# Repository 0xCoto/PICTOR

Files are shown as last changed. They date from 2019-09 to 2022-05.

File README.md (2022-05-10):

# PICTOR: A free-to-use Radio Telescope
PICTOR is an open-source radio telescope that allows anyone to observe the radio sky, using its convenient web platform for free: https://www.pictortelescope.com

The PICTOR Radio Telescope

The PICTOR Radio Telescope

## About PICTOR
PICTOR consists of a 1.5-meter parabolic antenna that allows anyone to make continuous and spectral (i.e. [hydrogen line](https://en.wikipedia.org/wiki/Hydrogen_line)) drift-scan observations of the radio sky in the **1300~1700 MHz** regime for free. 

The goal of this effort is to introduce students, educators, astronomers and others to the majesty of the radio sky, **promoting radio astronomy education**, *without* the need of building a large and expensive radio telescope. 

PICTOR is a **fully open source** (software & hardware) project.

## Northern Sky HI Survey obtained with PICTOR
PICTOR HI Survey

## Technical Details (Telescope Specifications)
**Telescope diameter:** 1.5m (4.92 ft = 59.05")  
**Focal Ratio (F/D):** 0.411 (prime focus antenna)  
**Beamwidth (HPBW @ 1420 MHz):** \~8.95° (*k* factor = 63.64)  
**Operating frequency range:** 1300\~1700 MHz ([L band](https://en.wikipedia.org/wiki/L_band))  
**Two-stage low-noise amplifier (LNA):** Gain: 30 ± 2 dB - Noise figure (NF): < 0.5 dB  
**High-pass filter:** -30 dBc below 900 MHz  
~~**Third-stage LNA (used as an in-line amplifier):** Gain: > 9 dB~~ *  
~~**Band-pass filter:** f_center = 1420 MHz (designed for [hydrogen line](https://en.wikipedia.org/wiki/Hydrogen_line) observations)~~ *  
**Instantaneous bandwidth (IBW):** up to 3.2 MHz (sufficient for spectral observations) *[to be upgraded to 30.72 MHz]*  
**Number of channels:** up to 2048 (for high frequency-resolution observations) *[to be upgraded to 16384]*  

*\*Deemed unnecessary hence removed*

## Telescope Block Diagram
Telescope Block Diagram

## PICTOR System Flowgraph
PICTOR flowgraph

## GRC Data Acquisition Flowgraph (old)
Data Acquisition Flowgraph (old)

## GRC Data Acquisition Flowgraph (4-tap weighted overlap-add (WOLA) Fourier transform spectrometer)
Data Acquisition Flowgraph

## Feedhorn Dimensions
Feedhorn dimensions

## S-Parameters
S-Parameter of the monopole inside the feed:
S-Parameter of the monopole

S-Parameter of the feedhorn (with rod) - **this should be the considered S-Parameter of the antenna in its entirety**:
S-Parameter of the feedhorn

Measured with the **Keysight N5221A PNA Network Analyzer (10 MHz~13.5 GHz)**:
Measurement of the monopole at the lab
Measurement of the feedhorn at the lab

## Example Observation
Example Observation

## Wish to observe with PICTOR?
Take a look at the [PDF guide](https://www.pictortelescope.com/Observing_the_radio_sky_with_PICTOR.pdf) containing all the information you need to know in order to conduct your first observation of the radio sky!

<p align="center">
  PICTOR Telescope Logo
</p>

## A description/role for each file
File | Description
--- | --- 
`observe.py` | Listens for observation requests & conducts observations
`plot.py` | Produces plots from observation data
`plot_hi.py` | Produces HI-tailored plots (i.e. +calibrated spectrum) from observation data
`id_history.txt` | Serves as an observation ID history database
`fft_integration.grc` | [GRC](https://wiki.gnuradio.org/index.php/GNURadioCompanion) Flowgraph previously used for the recording and processing of the data
`top_block_old.py` | Embedded Python Block for `fft_integration.grc`
`pfb.grc` | [GRC](https://wiki.gnuradio.org/index.php/GNURadioCompanion) Polyphase Filterbank Flowgraph for efficient data acquisition
`top_block.py` | Embedded Python Block for `pfb.grc`
`observe.php` | Includes server-side PHP code for [/observe](https://www.pictortelescope.com/observe)
`Waveguide.stl` | STL file for feedhorn visualization

## Credits
**PICTOR** was built by **[Apostolos Spanakis-Misirlis](https://www.github.com/0xCoto)**.

Special thanks to **Dr. Cameron Van Eck** for his thorough guidance throughout the development of PICTOR, the **[Telecommunication Systems Laboratory](http://tsl.ds.unipi.gr/)** of the [Department of Digital Systems](https://www.ds.unipi.gr/en/) at the [University of Piraeus](https://www.unipi.gr/unipi/en/) for allowing us to conduct decisive antenna measurements, the [Dwingeloo Radio Observatory](https://www.camras.nl/en/) (**Paul Boven** & **Dr. Cees Bassa**) for helping with the recording & the plotting of the data, **[Vasilis Spanakis-Misirlis](mailto:meiko_dew@hotmail.com)** for his engineering assistance, Konstantinos Bakolitsas for his support and **[ynk](https://www.github.com/ynk)** & **[Tino](https://www.github.com/RononDex/)** for their back-end contribution to `observe.php`.

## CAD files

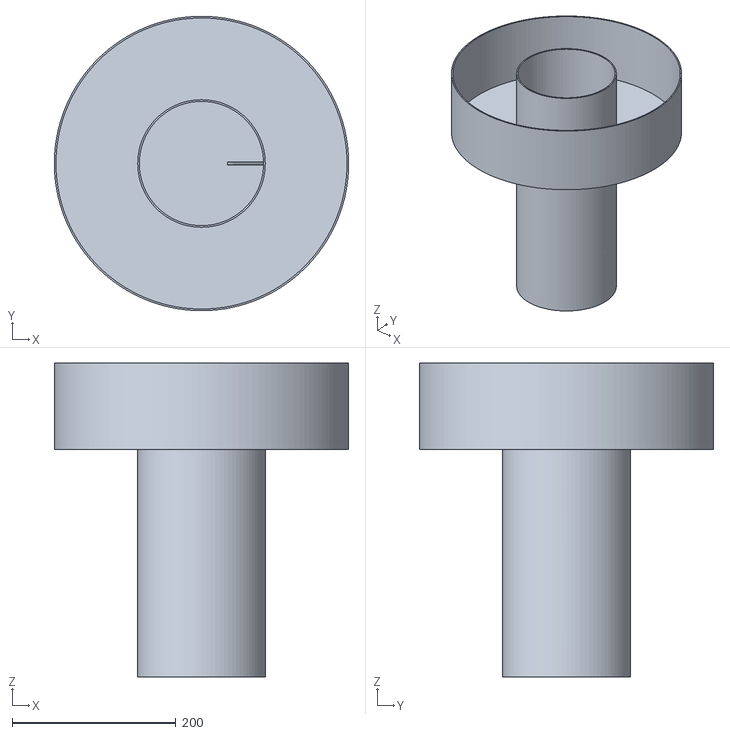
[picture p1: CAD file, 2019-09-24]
Waveguide.stl
360.0 x 359.9 x 384.0

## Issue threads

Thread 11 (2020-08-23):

Send Raw Data

ministerofsillywalks, 2020-08-23:
Hi! One thing that I've felt was missing from the PICTOR experience was the ability to have the raw data. It's nice to quickly see the results of an observation, but it's hard to do precise analysis of the data. Would it be possible to have an option when you submit the obs. request to receive the raw data file, perhaps in a csv file, for each of the graphs?

0xCoto, 2020-08-23:
Hey, thanks for your feedback! I suppose that's possible, but it requires a bit of work from my side (feel free to contribute if you'd really wanna see that - hint: you'll have to add a relevant checkbox option to [`observe.php`](https://github.com/0xCoto/PICTOR/blob/master/observe.php) and edit [`observe.py`](https://github.com/0xCoto/PICTOR/blob/master/observe.py) to permit the server (pictortelescope.com) and the client (telescope) to share that parameter).

However, I am more than happy to send you the raw data of your observation, given your Observation ID. If you look at [line 120](https://github.com/0xCoto/PICTOR/blob/master/observe.py#L120-L164) of `observe.py`, you'll notice that I keep a copy of every observation's raw data (`.dat` file), so if a user wishes to process, analyze and inspect their data in greater detail, they have the freedom to do so.

The reason I don't include the `.dat` in the original email is to avoid confusion, as many users are unfamiliar with Python to run `plot.py`, nor do they understand how radio astronomy digital signal processing/data analysis works.

But if you think this is worth implementing, it's an easy code change, so I could probably find some time to implement it.

ministerofsillywalks, 2020-08-24:
I have an idea about how to do this, but I have a couple of questions about the system:
1. If all the observation parameters are stored and read from `last_obs.txt`, what is `last_obs_duration.txt` used for?
2. Can I use a package that has not been used yet? specifically, pandas.
Thanks!

0xCoto, 2020-08-24:
1. Short answer: user privacy. The telescope fetches `last_obs.txt`, but the website (`observe.php`) needs to fetch the last observation request datetime and duration. This was initially used to check if an observation was already running to prevent clogging from observation requests. The reason it doesn’t just fetch `last_obs.txt` is because that file includes the email address of the observer, which is sensitive data, which is obviously a problem, both ethically and legally (GDPR).

2. For plotting? You can use anything you like of course, but I’d be curious to know what you’d like to play with that `plot.py`/`plot_hi.py` and numpy doesn’t already provide.

ministerofsillywalks, 2020-08-24:
I want to use pandas to save csv files because it allows you to save with each data array in a labeled column easily, whereas if I just used numpy to write csv's it would be messier. Taking it a step back, I would rather make csv files in addition to the .dat file because the csv's are easier to open. Basically I'm trying to make it as easy as possible to get good data.

P.S. If it's not too big a problem, could you send me the dat file for observation 55275982 so I can test my code? This is one of my own observations. Thanks!

0xCoto, 2020-08-25:
You should be able to do this with numpy as well. I've implemented something like this for `.txt`, but you should be able to adjust it for `.csv` formatting as well pretty easily, but feel free to use whatever is more convenient for you of course.

Example snippet for saving the calibrated spectrum (you place this in `plot_hi.py`):
```python
np.savetxt('freq.txt', freq, delimiter='\n', fmt='%1.3f')
np.savetxt('snr.txt', estimate_S_N_simple(spectrum, mask), delimiter='\n', fmt='%1.3f')
```

I've uploaded your `observation.dat` file [here](https://gofile.io/d/d4AVVo).

ministerofsillywalks, 2020-08-26:
Thanks for the file! I just created the pull request.

Closed 2020-09-20.

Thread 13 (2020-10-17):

Transpose data in CSV files

andy8025, 2020-10-17:
Change the way data are stored in __data_spectrum.csv__ and __data_time_power.csv__ files that are emailed to user. Transpose rows and columns - to store samples in rows instead of columns.

Current layout:

foo|1000|1001|1002|...
------------ | ------------- | ------------- | ------------- | -------------
__bar__|__2000__|__2001__|__2002__|__...__

Proposed layout:

foo|bar
------------ | -------------
__1000__|__2000__
__1001__|__2001__
__1002__|__2002__
__...__|__...__

Current CSV file layout prevents LibreOffice Calc from reading all the data. LibreOffice error: "The data could not be loaded completely because the maximum number of columns per sheet was exceeded".

andy8025, 2020-10-17:
Made changes to __plot.py__ and __plot_hi.py__ to save the new transposed CSV files, in addition to the original CSV files. Did not modify the code in __observe.py__ that emails the CSV files.

Don't know how to check what Python libraries are available on the actual telescope system.  I see that NumPy is available, hope that Pandas is available as well :)

ministerofsillywalks, 2020-10-17:
When I first did this, I wanted to use pandas to make the CSVs the way you want them, @0xCoto asked that I stick with just numpy instead.

ministerofsillywalks, 2020-10-17:
You might be able to use np.transpose() https://note.nkmk.me/en/python-numpy-transpose/ without importing pandas.

ministerofsillywalks, 2020-10-18:
You shouldn't need pandas because you can do the transposition without reopening the csvs, just do it before they are saved.

andy8025, 2020-10-18:
Ok, I can try it in numpy.  Is it possible to get a copy of __observation.dat__, so that I may generate the __data_freq_zmean__ and __data_t_w__ numpy arrays?

0xCoto, 2020-10-18:
Thanks for the PR, just approved! The changes have been applied to the telescope, so feel free to try it out. :)

Closed 2020-10-18.

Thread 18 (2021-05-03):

Time Series File showing Power to 3DP

davewyers, 2021-05-03:
Hi There

Love your work.  I have a 2.3M dish that I have planning on going live with VIRGO in a couple of weeks, meanwhile I was generating some data with PICTOR to play with.

I ran a test on Pictor and when I looked at the Time Series data it appears that the Relative Power column is only showing 3DP "0.010" across all time time slots.  I am assuming that Column 1 is Time & Column 2 is Relative Power.

The graph is displaying values to 6DP.

See below.

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

0xCoto, 2021-05-03:
Thanks for the feedback!

davewyers, 2021-05-04:
Perfect, I have just tested and can confirm the fix.

What is the best way to interact around PICTOR & VIRGO outside of issues, do you have a user forum?

Regards
Dave

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

0xCoto, 2021-05-05:
There used to be a Discourse page (forum) for discussions related to PICTOR and (radio) astronomy, but maintenance was a bit costly (mostly in terms of my time, and partially hosting costs as CPU allocation is higher hosting more web pages online).

davewyers, 2021-05-06:
Ok understood, thanks

Closed 2021-05-06.

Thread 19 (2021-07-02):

Comment batch (Richard K Collins)

0xCoto, 2021-07-02:
Full list of comments here: https://theinternetfoundation.net/?p=1742

0xCoto, 2021-07-02:
My response to every single comment is stated below. I skipped some minor parts because virtually identical replies have already been provided. Thanks to Richard Collins for the comments. Anyone wishing to resolve some of the commented requests is welcome to submit a pull request with the corresponding changes/additions.

---

> Please leave the settings and all form fields. Don’t clear them. Just leave them the same as the last observation.

This is not very easy if you consider there are many unique observers who wish to run observations with varying parameters. Leaving them the same as the last observation could introduce a lot of confusion between unique users visiting the website after one's observation. PICTOR does not make use of cookies for such things, but perhaps it could. It's a technical challenge though, and I do not know how much effort is worth putting into.

> I am having to re-enter them ever time I make a request.  I am making series of requests.  Many people might.

A simple trick to achieve this is to click `Observe` (the button), opening it in a new tab. This will submit the request, while leaving your fields in place. Maybe this helps as a quick solution.

> Tell them how many files they will receive, how many records per file, and the units and purpose.

The fundamentals regarding the expected results and how to interpret them are described in the [introductory PICTOR PDF](https://pictortelescope.com/Observing_the_radio_sky_with_PICTOR.pdf), but I agree that the CSV results may not be very clear, partially due to missing headers. Most users only look at the image plots though (not that this is a justification for lacking clarifications, but the point of PICTOR is to make observations easy for users with little to no experience, who just wish to see the results without much further processing work). As for the units, "relative power" highlights that the power is not calibrated to Kelvins or Janskys. This is imposed by an instrumentation limitation (requiring external noise source). But absolute measurements don't appear to be a necessity for most users who simply wish to detect clouds of neutral hydrogen etc.

> Put column headers in the csv files. You can add headers to explain the columns by using a # in the first column to indicate header...

I agree this would be useful.

> ...then use tab separators. Use tab separators through out. That is the default for Excel, even if they still say “csv”.

Virtually all CSV-formatted files I have seen use commas and not tabs. Transforming to tabs would annoy developers and programming libraries that are used to the more traditional **comma-separated** value format. I also don't understand what "default for Excel" means, because importing and exporting to CSV (with commas) is fully supported by common spreadsheet tools as far as I'm aware.

> CSV is NOT a standard.

The objective is to mimic a format as closely to what most users are familiar with as possible. The goal is for the interpretation of the results to be clear to the user and for the data to be easily parsable to other data-analysis software. This is also completely possible with **tab-separated** values (TSV), but less common than CSV handling.

> When you copy and paste from Excel, it is tab separated – because then you don’t have to write infinite recursion for quoted strings. Just a single tab between fields, line feed separating records. Human and Excel readable header lines.

As mentioned, you can import from and export to CSV with common spreadsheet software like Excel without problems. What format Excel decides to encode your clipboard in when you copy cells appears irrelevant, because it is intended for transferring data within the same type of software (spreadsheets). The incompatibility with programmatic data analysis (e.g. using Python libraries) becomes more apparent when trying to deal with TSV instead of CSV-formatted files.

> Show the consequences of choices. How many data points in the time series will be given for the selection?

This could be displayed with JavaScript on the spot; requires work though.

> What are the limits for your processor?

The available results have all been tested and supported, so the user does not need to worry about this to be worth mentioning.

> How fast could you provide small FFT records.

I assume this refers to the time-series delta t (Δt). There is a limit put in place (number of bins ≥ 100). The users cannot violate this and are informed if they try setting a value lower than that. This ensures that the machine does not struggle with processing and analyzing very large files, or uploading large chunks of data over the network.

> You show the waterfall but do not provide that time series.

Time-series (power vs time) is displayed at the bottom. If you are referring to raw time-domain I/Q information, each observation would be dramatically larger in data size, which would cause problems partially mentioned in the previous statement. The total size of an observation would be equal to `2` [I + Q channels] x `sample_rate` [samples/sec] x `8` [bits] x `duration` [sec].

> If someone is looking at adjacent frequencies to the center, you are only providing summary statistics.

It is not clear at all what this comment implies, nor what 'summary statistics' are. All information the user requires for typical hydrogen line observations is there, including the waterfall, average spectrum and calibrated (passband-corrected) spectrum.

> “Raw” means the original readings. What you are providing is a summary statistics in your time series. A computed value based on the FFT, which comes from the sampled time series data. “Raw” would be the 2.4 MegaSamplesPerSeconds or whatever the user selected. It could be requested — without FFT processing.

"Raw" may sound misleading to hint I/Q data, but it is in no way a strictly incorrect term. "Raw" is displayed in the sense that the data attached in the CSV are less processed. This includes the calibration/OFF spectrum (not calibrated), permitting the user to do manual passband calibrations. Feel free to propose a more appropriate adjective than "raw" that is more clear and I'll implement the modification.

> You might want to call the time series you provide now “Power time series” or “Relative Power time series”

The plot title ('Average Power vs Time') implies that all frequency channels have been averaged at every time instance. The Y-axis ('Relative Power') implies the power is not calibrated to Kelvins/Janskys.

> But you need to make an effort to put it on an absolute basis.

As mentioned earlier, this requires special hardware equipment such as a noise diode, with which PICTOR is not equipped. Running flux calibrations by observing astronomical radio sources is not very easy with small-aperture antennas, and virtually impossible without an antenna rotator/steering equipment (PICTOR is a stationary instrument intended for drift-scan observations).

> Your histogram for “Total Power Distribution” could be useful as a summary time series. That could be an option instead of FFT. It can be computed and stored very fast, and could give a summary of the counts of levels (and first and second derivatives) many times a second. For 2.4 Msps, groups of 10,000 samples can be summarized by max, min, mean, mode and range. And counts by level. 10,000 samples per statistical summary record at 2,400,000 sps is 240 statistical frames per second.

The total power distribution plot is not very meaningful for most users, but is available to demonstrate Johnson–Nyquist noise, and that thermal noise follows a Gaussian amplitude distribution. It could also be used for investigating time-varying RFI vs internal noise, but that's rarely something being looked into.

> I think you have many times no one is online. I recommend you run continuously and put summaries of 24 hours online. And have that data available for download.

There could be an open archive, but hosting it requires effort, maintenance work, and cost. A cooling solution might also need to be in place if the telescope is running 24/7 (which does not make a lot of sense to me when the point is for the user to experience observing the radio sky first-hand and collecting real and unique-feeling data).

> If people are going to learn to analyze radio telescope data, they are not going to learn much, except operator clicks and settings, with smal samples.

Decreasing simplicity and increasing difficulty decreases accessibility. The objective is to **introduce** as many people to radio astronomy as possible. Very few people have reached out and expressed an interest in thoroughly and manually analyzing data in a very custom fashion. If an educational institute, however, wishes to make things more in-depth for their students, we are more than happy to make the process more thorough by providing only CSV data for example. In fact, a university recently reached out and asked us to elaborate very little to their students, so they learn by playing around and experimenting with the system, and next year we're planning to make much more of the process manual for another more advanced course.

> [...] You cannot point, but you can record everything and index events.

There is no research, nor educational interest behind observing 24/7.

> The true value of sensors is when you use arrays of them to look at something together. You only see the zenith in a small disk or zone. Anyone at your latitude anywhere on earth will see close to the same with time offsets. If the sources are stable, then stacking the results from many sensors will begin to strip local variations. If you record continuously the path of the sky you see will repeat fairly closely.

Building a community-maintained large network of small-aperture radio telescopes sounds cool in theory, but unveils many technical and non-technical challenges in practice. And more importantly, it is not clear if there's any real research you can do (or any interesting education for that matter).

> During the day there will be clouds, and those clouds can also be tracked. If one drifts overhead that should be observable.

Clouds are not observable at these wavelengths - they are transparent to radio waves.

> Put “donate” and “support” online.

I was extremely fortunate to discover great teachers wishing to share their knowledge on astronomy and microwave engineering, dedicating countless hours at no cost, and I feel that it is a moral obligation for me to give back similar opportunities to others. I have never been interested in receiving any donations from the users; I do not want them to pay anything in return to learning. I could accept funding by independent grant programs (and it would help), but not by the observers themself.

> And try linking to all related individuals and groups doing the same thing.
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

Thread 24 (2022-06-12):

How to configure position

Firestar-Reimu, 2022-06-12:
For example, I want to observe the 21cm line from the galaxy center, how to configure PICTOR to aim at the Galaxy Center

0xCoto, 2022-06-13:
The telescope is not equipped with a rotator — it's fixed pointing to the zenith, so it works as a drift-scan telescope.

Closed 2022-06-26.

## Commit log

2019-08-26 Added 3D Model of the Waveguide
    [Waveguide.stl]
2023-06-21 Added functionality (#25)
    * Add files via upload
    Using this program you can:
    1. Perform an observation from your terminal, without using a browser
    2. Schedule an observation for a day in the current month of the current year
    3. Schedule and perform consecutive observations with a set interval time
    * Update obs_scheduler.py
    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
